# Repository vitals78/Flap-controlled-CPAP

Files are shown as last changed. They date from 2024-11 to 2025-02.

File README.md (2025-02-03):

# Flap-controlled-CPAP
The design of the print cooling fan, controlled by a flap, allows more precise cooling of overhangs.
1. Controlling the airflow with a flap allows for more precise cooling of overhangs. This enables the printing of more durable parts, as there is no overcooling caused by the prestart of the blower fan. Overcooling is also eliminated due to the lack of impact from the rotor’s inertia.
2. The WS7040 fan begins rotating at 18-21% power, which may be excessive in some cases (for example, printing ABS, ASA). In contrast, flap-controlled airflow can start at just 1%.
3. The rotor’s inertia in the cooling fan has no significant impact, enabling the use of various fan types, including centrifugal blowers, Roborock vacuum cleaner fans, and powerful server fans.
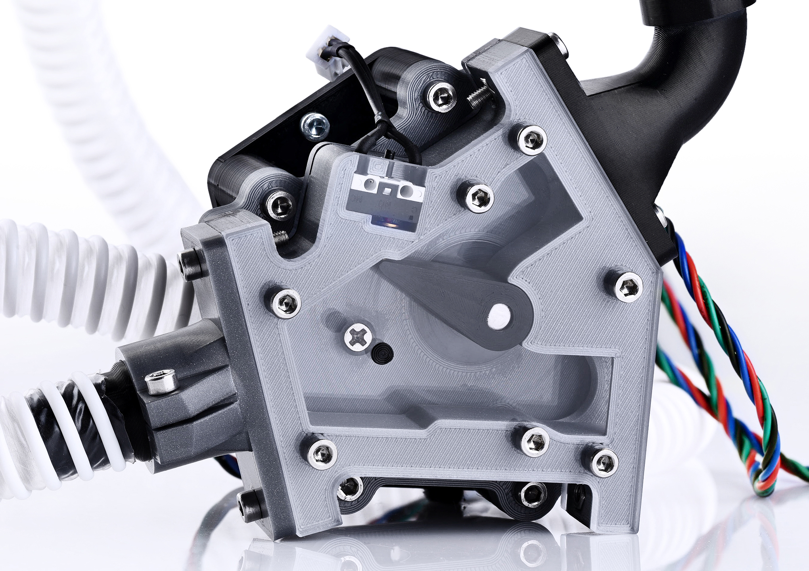
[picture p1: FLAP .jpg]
flap

https://www.youtube.com/watch?v=osWIlmkUGPM&t=235s

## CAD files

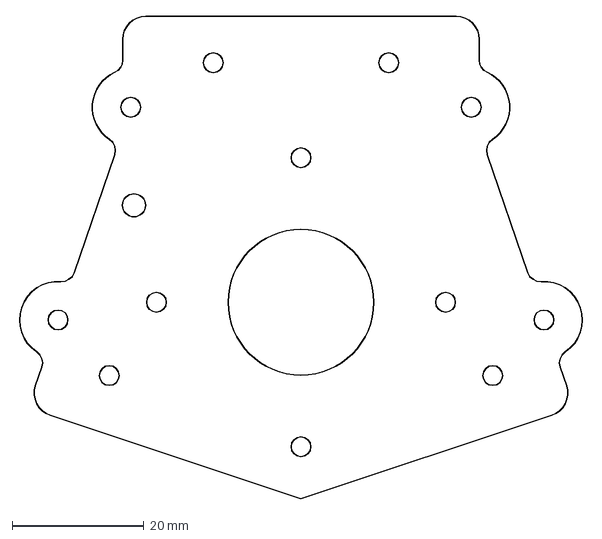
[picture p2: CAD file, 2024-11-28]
DXF for CNC milling/Motor mount.dxf
86.4 x 73.2 mm

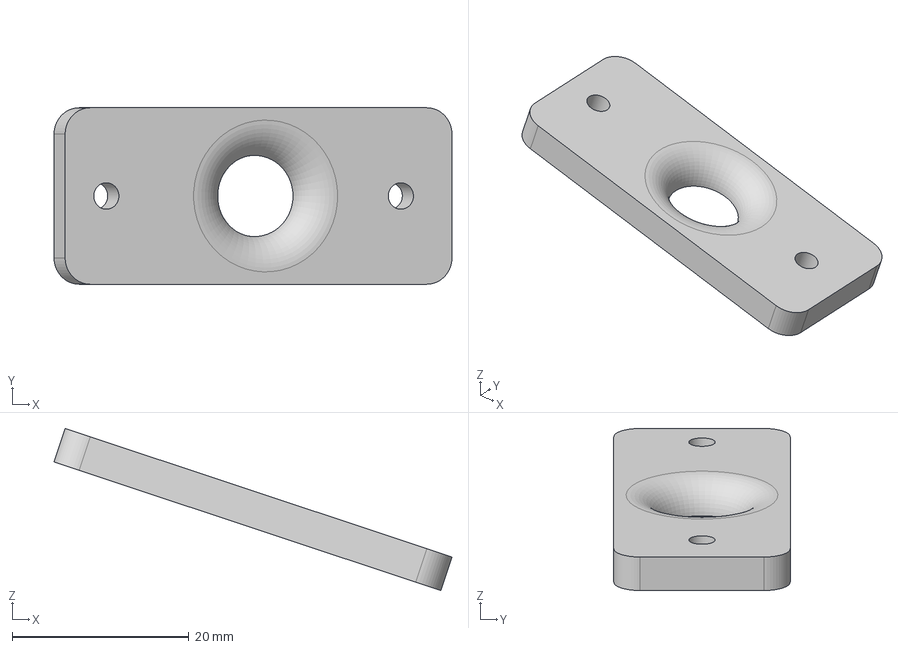
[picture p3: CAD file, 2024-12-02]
STEP/piece with hole.step
45.1 x 20.0 x 18.4 mm

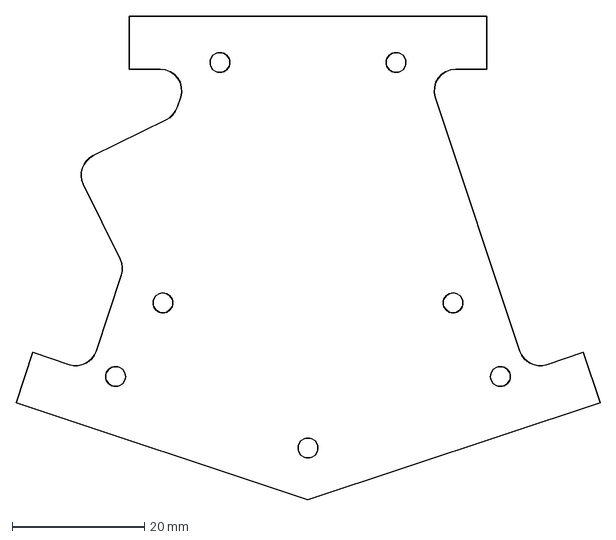
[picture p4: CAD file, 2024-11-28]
DXF for CNC milling/Top cover.dxf
88.2 x 73.0 mm

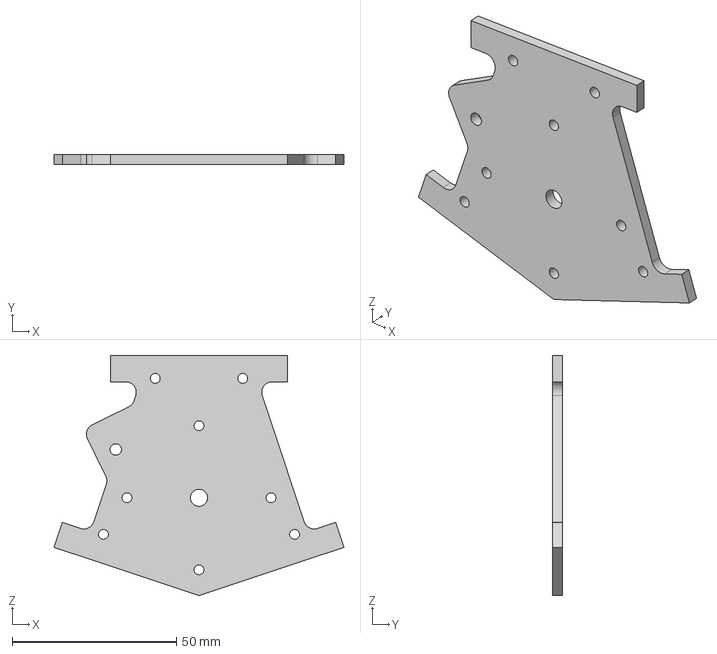
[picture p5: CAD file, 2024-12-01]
STEP/Bottom cover.step
88.2 x 3.00 x 73.0 mm

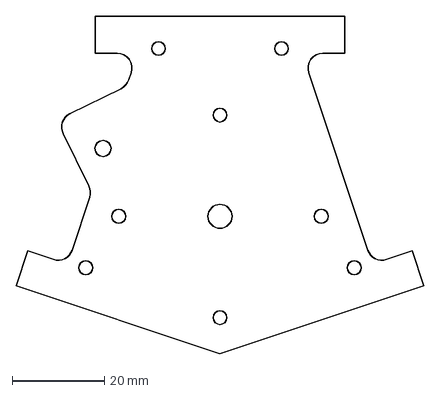
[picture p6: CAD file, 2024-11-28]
DXF for CNC milling/Bottom cover.dxf
88.2 x 73.0 mm

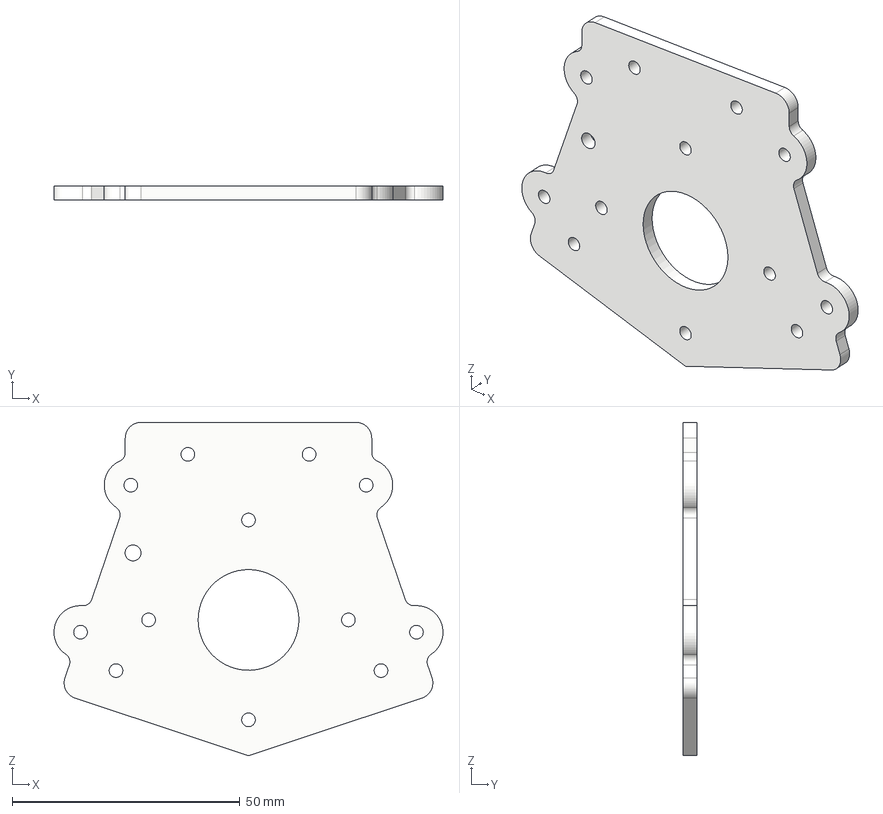
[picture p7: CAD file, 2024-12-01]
STEP/Motor mount.step
85.3 x 3.00 x 73.2 mm

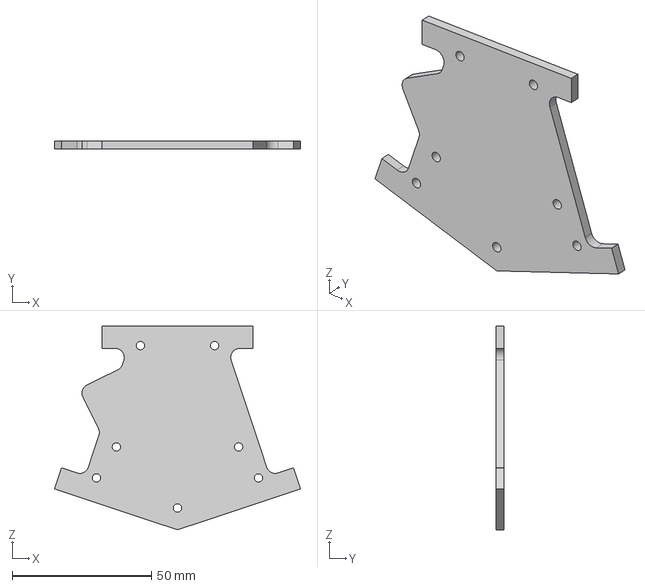
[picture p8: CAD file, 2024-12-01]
STEP/Top cover.step
88.2 x 3.00 x 73.0 mm

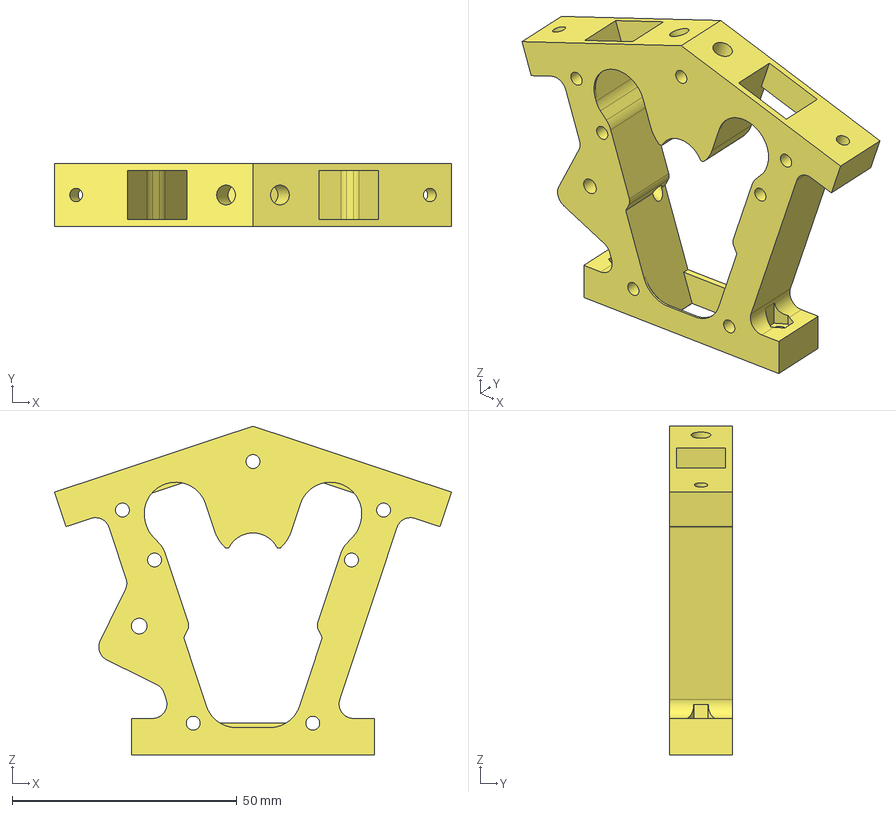
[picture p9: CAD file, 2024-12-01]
STEP/Frame.step
88.4 x 14.0 x 73.2 mm

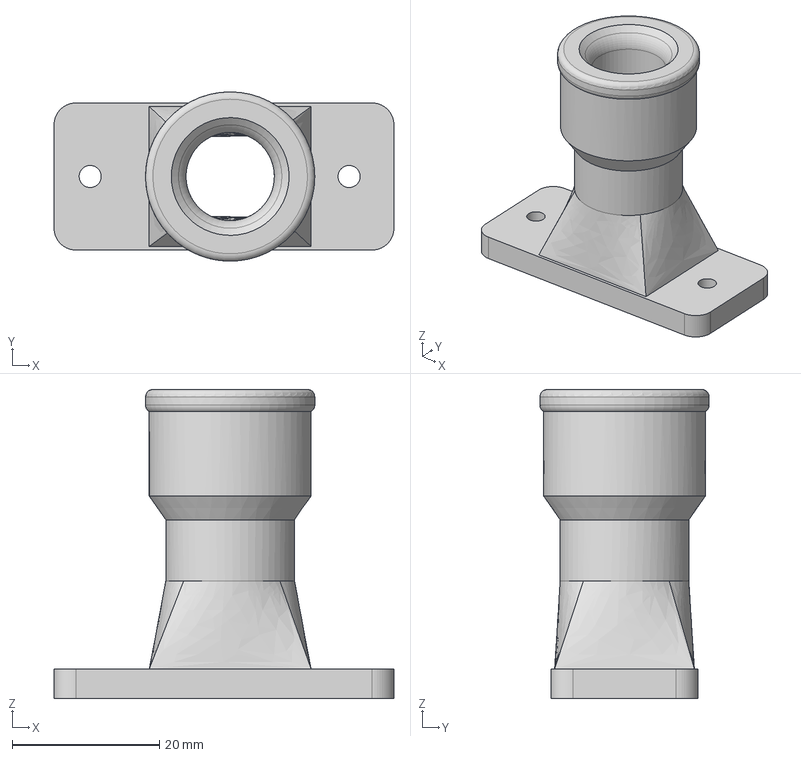
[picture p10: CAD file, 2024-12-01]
STEP/fitting1.step
46.2 x 23.0 x 42.0 mm

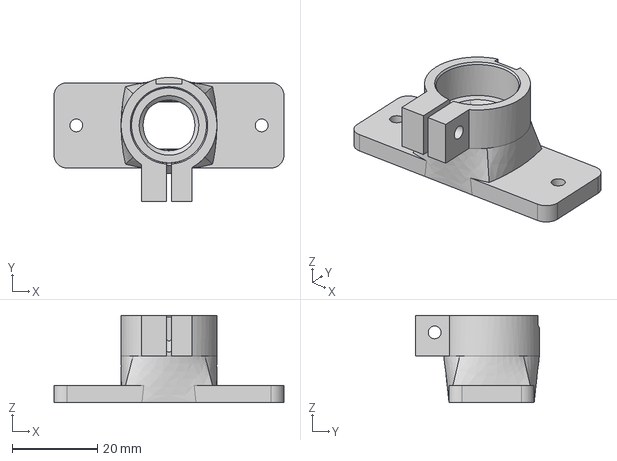
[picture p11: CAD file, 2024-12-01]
STEP/fittingCPAP.step
54.0 x 29.1 x 20.5 mm

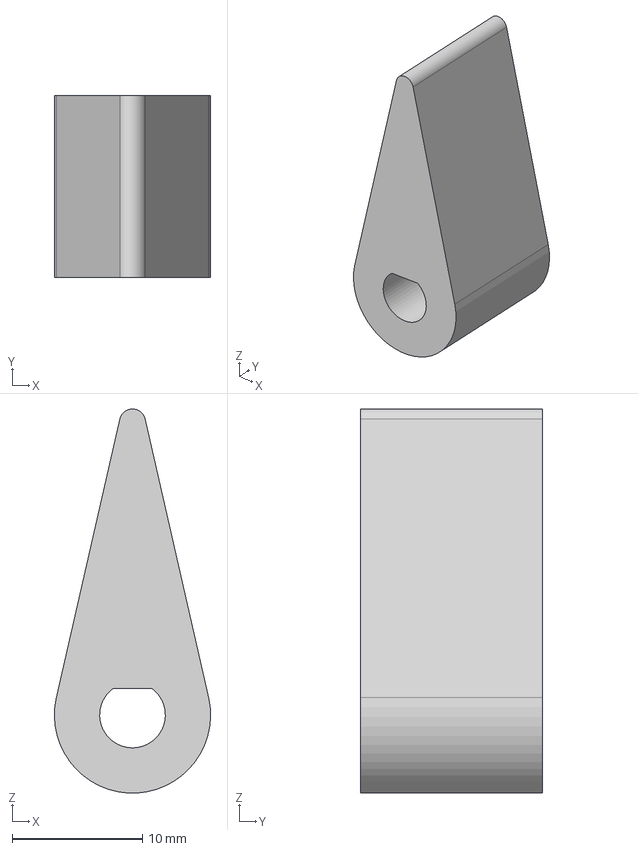
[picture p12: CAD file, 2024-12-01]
STEP/flap.step
12.0 x 14.0 x 29.5 mm

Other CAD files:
STL/Bottom cover.stl
STL/Flap.stl
STL/Frame.stl
STL/Motor mount.stl
STL/Top cover.stl
STL/fitting1.stl
STL/fittingCPAP.stl
STL/piece with hole.stl

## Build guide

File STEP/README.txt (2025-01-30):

Filters purchased on Aliexpress have different lengths, so
the mount needs to be adjusted separately for the filter.
In addition, the outlet of the WS7040 fan is not perfectly
round, so the fitting in my case is made elliptical.
Therefore, the downloaded STEP will need to be seriously edited
to your fan opening dimensions, and the filter length. Also, STEP
file includes a new fan duct. You can check its detailed test here: 
https://discord.com/channels/829828765512106054/1019188485174865920/threads/1326262105917362279 
https://www.youtube.com/shorts/48ocllo4TVM

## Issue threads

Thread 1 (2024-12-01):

Step files are seperate, one is missing

HeavilyModdedEnder3, 2024-12-01:
In the build video, there is shown the excess piece (which has to be the same size as the outlets on the toolhead), but it is missing in the step files. Also, by exporting the whole assembly, including screws and fasteners, as one step file, it would be much easier to work with (like the voron m4 step file, etc.)

HeavilyModdedEnder3, 2024-12-04:
Also, with the main body, it is mirrored (unlike the videos)

HeavilyModdedEnder3, 2024-12-04:
Also, here's a quick parametric excess hole piece! [https://cad.onshape.com/documents/d675051976fc277f694d7d76/w/4d229b8498afa52c8f553c70/e/6a29c4191a7c8ce2d0ef530b](url)
Just change the configuration called OutletSize to the area of the outlet duct in mm^2

vitals78, 2024-12-05:
This detail can be mirrored. Depends on preferences.
I'll do BOM later when I have some time.

jefedahmer, 2025-01-30:
Have you had a chance for a BOM?

vitals78, 2025-02-01:
Sorry I still can't find time for this.

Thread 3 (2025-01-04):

Existing command 'M106' not found in gcode_macro rename

oMTEo, 2025-01-04:
When I try to implement your M106 and M107 macros, following error occurs

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

oMTEo, 2025-01-04:
After hours of research I got it working now :)

The option Fake-Fan was missing (found it in your Video), its not in your Flap_stepper.cfg

Closed 2025-01-04.

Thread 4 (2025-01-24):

supply bracket assembly like in Photos

qp1306, 2025-01-24:
Any chance you can supply the step file/s for the bracket assembly thats in the photos?
Thanks

vitals78, 2025-01-28:
Hi. The mounts in the photo are only suitable for my custom version of vzbot.
Also, the filters bought on aliexpress have different lengths, so
the mounts need to be adjusted individually for the filter.
In addition, the outlet of the WS7040 fan is not perfectly round,
so the fitting in my case is made elliptical. I will upload the files soon, but they will need to be seriously edited to
install your version of the filter fan and mount.

vitals78, 2025-01-30:
STEP files added

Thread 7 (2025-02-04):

FLAP CPAP+new blow nozzle 16.step file - part: fitting (top left u shaped fitting)

jefedahmer, 2025-02-04:
When exported as an stl, the tapered end that connects to the tube, it prints layers 42-51 as solid. I'm unfamiliar with CAD, so i'm not sure what to look for in the cad file.

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

vitals78, 2025-02-04:
Hi. I exported to stl and everything is ok.

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

vitals78, 2025-02-04:
Your image shows low stl detail. This may be the problem. Use a higher quality when exporting to stl

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

jefedahmer, 2025-02-04:
I will give this a try later this evening. Thanks

jefedahmer, 2025-02-05:
Exported using AutoCAD with no issues. I appreciate your help, thank you! Rough build until I get some the clear top and bottom plates.

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

warpedscale, 2025-02-14:
Kudos to you @jefedahmer for installing this on a Merc. I did the same thing. 😁

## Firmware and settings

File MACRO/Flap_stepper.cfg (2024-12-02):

[manual_stepper flap_stepper]
step_pin: PE4
dir_pin: !PG0
enable_pin: !PG1
microsteps: 16
rotation_distance: 1150
velocity: 4000
accel: 85000
endstop_pin: PD7

[tmc2240 manual_stepper flap_stepper]
cs_pin: PF15
interpolate: false
run_current: 0.8
hold_current: 0.6
spi_software_mosi_pin: PB5
spi_software_miso_pin: PB4
spi_software_sclk_pin: PB3

[fan_generic exhaust_fan] 
pin: PA3


[gcode_macro _SET_FLAP_ENABLED]
variable_enabled: 0
gcode:
    {% set enabled=params.ENABLED|int %}
	{% set flap_enabled=printer["gcode_macro _SET_FLAP_ENABLED"].enabled|int %}
	{% if enabled!=flap_enabled %}
		SET_GCODE_VARIABLE MACRO=_SET_FLAP_ENABLED VARIABLE=enabled VALUE={enabled}
		{% if enabled==1 %}
			MANUAL_STEPPER STEPPER=flap_stepper ENABLE=1
			MANUAL_STEPPER STEPPER=flap_stepper MOVE=-255 STOP_ON_ENDSTOP=1 SPEED=30
			MANUAL_STEPPER STEPPER=flap_stepper SET_POSITION=0
		{% else %}
			MANUAL_STEPPER STEPPER=flap_stepper MOVE=0
			MANUAL_STEPPER STEPPER=flap_stepper ENABLE=0
		{% endif %}
	{% endif %}

[gcode_macro M106]
rename_existing: M106.1
gcode:
    {% if params.P is defined %}
        {% if params.P|int == 3 %}
            {% if params.S is defined %}
                {% if params.S|int == 255 %}
                    {% set realspeed = 1 %}
                {% else %}
                    {% if params.S|int == 0 %}
                        {% set realspeed = 0 %}
                    {% else %}
                        {% set realspeed = params.S|float/255 %}
                    {% endif %}
                {% endif %}
            {% else %}
                {% set realspeed = 1 %}
            {% endif %}
            SET_FAN_SPEED FAN=exhaust_fan SPEED={realspeed}
		{% elif params.P|int == 1 %}
			_SET_FLAP_ENABLED ENABLED=1
			{% if params.S is defined %}
				MANUAL_STEPPER STEPPER=flap_stepper MOVE={params.S} SYNC=0
			{% else %}
				MANUAL_STEPPER STEPPER=flap_stepper MOVE=255 SYNC=0
			{% endif %}
		{% else %}
			M106.1 {rawparams}
        {% endif %}
    {% else %}
		_SET_FLAP_ENABLED ENABLED=1
        {% if params.S is defined %}
          MANUAL_STEPPER STEPPER=flap_stepper MOVE={params.S} SYNC=0
        {% else %}
          MANUAL_STEPPER STEPPER=flap_stepper MOVE=255 SYNC=0
        {% endif %}
    {% endif %}

[gcode_macro M107]
rename_existing: M107.1
gcode:
    {% if params.P is defined %}
		{% if params.P|int == 3 %}
			SET_FAN_SPEED FAN=exhaust_fan SPEED=0
		{% elif params.P|int == 2 %}
			M107.1 {rawparams}
		{% elif params.P|int == 1 %}
			MANUAL_STEPPER STEPPER=flap_stepper MOVE=0 SYNC=0
		{% endif %}      
    {% else %}
      SET_FAN_SPEED FAN=exhaust_fan SPEED=0
	  MANUAL_STEPPER STEPPER=flap_stepper MOVE=0 SYNC=0
	  _SET_FLAP_ENABLED ENABLED=0
      M107.1 {rawparams}
    {% endif %}
